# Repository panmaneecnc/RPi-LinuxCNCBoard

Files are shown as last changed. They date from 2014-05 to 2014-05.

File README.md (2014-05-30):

RPi-LinuxCNCBoard
=================
These files are part of the rpi_rboq project.
driver: Contains all the files related with the HAL(Hardware Abstraction Layer) driver programmed to integrate rpi_rboq to LinuxCNC.
PCB: Contains all the files of the PCB design. To open this files you required Eagle 6.5.0 version, available from: http://www.cadsoftusa.com/
presentation: Contain the presentation designed for oral defense.
raspberry_images: Contains the images compiled during the work using Xenomai and the PREEMPT-RT patch.
report: Contain the full report in PDF format.
testing: Contain all the testing code and libraries written by this work.

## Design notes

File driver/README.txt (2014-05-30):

To install this driver, execute the following command in Linux console:
sudo comp --install --install-documentation hal_rpirboq.hal

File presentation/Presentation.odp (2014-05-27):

## Beijing University of Posts and Telecommunications 北京邮电大学

CONTROL BOARD FOR CNC SYSTEMS BASED IN LINUX

Author: Rodolfo Boris Oporto Quisbert

Final Project

## Contents

- 1 Introduction
- 2 Background and technologies
- 3 Design and implementation
- 4 Results
- 5 Conclusions and future work

## 1 Introduction

- Project motivation
  - Try to make a fully functional control board for CNC systems.
    - In the last years, this systems have attracted the attention of many groups, interested especially in 3D printers.
  - Research about Open Source solutions a its characteristics.
    - Raspberry-Pi, LinuxCNC, Xenomai, RepRap, Raspbian.

## 2 Background

- Raspberry Pi
  - Raspberry-Pi is a low cost fully-functional computer, based in BCM2835 SoC from Broadcom.
  - This board was developed to be used as part of an educational program in UK.

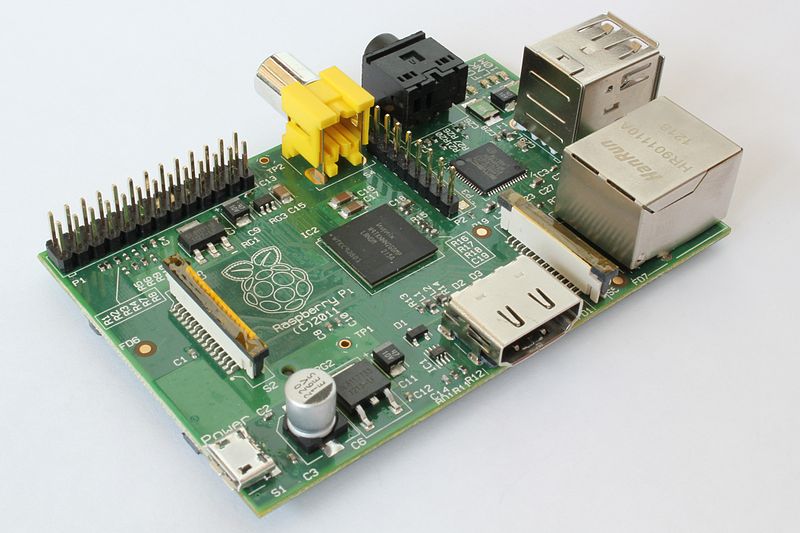
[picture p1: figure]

## 2 Background

- Raspberry Pi
  - Low cost (~300RMB)
  - Huge community.
    - Support.
    - Docummentation.
      - Blogs, papers, internet forums, books.

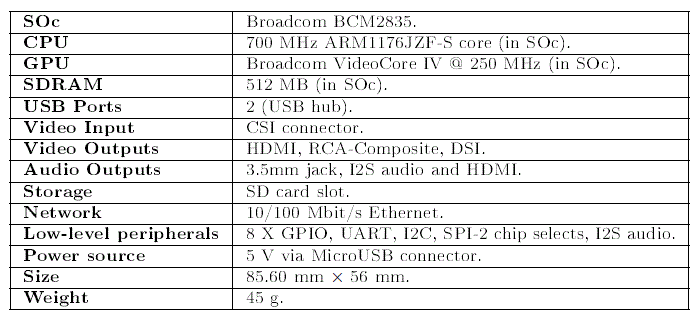
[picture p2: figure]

## 2 Background

- Real time under Linux
  - PREEMPT_RT patch
    - Preemption: Preemption is the interruption of a computer process without its cooperation
    - How does it work?
      - Making in-kernel locking-primitives.
      - Critical sections protected.
      - Implementing priority.

## 2 Background

- Real time under Linux
  - Xenomai
    - Xenomai is a real-time development framework cooperating with the Linux kernel.
    - API skins: native, POXIS, RTDM, pSOS
    - Two spaces
      - Kernel space: Hard real-time applications
      - User space: Real-time applications

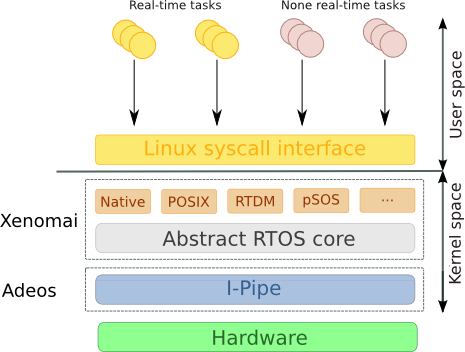
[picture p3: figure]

## 2 Background

- Real time under Linux
  - Why Xenomai?
    - Xenomai has a well documented API with different skins.
      - Examples, internet forums, API html documentation.
    - There is experiences with Xenomai running in Raspberry-Pi and LinuxCNC.
    - Official Xenomai patch for Raspberry-Pi.

## 2 Background

- LinuxCNC
  - Software collection for CNC machines. Former know as EMC.
  - Hardware Abstraction Layer
    - LinuxCNC use software components know as Hardware Abstraction Layer (HAL)
    - The developer can abstract from the details inside these blocks and use it like Symulink block.

## 2 Background

- LinuxCNC
  - Hardware Abstraction Layer
    - Some very important HAL components
      - RT Threads: hard real time thread which can be used to perform HAL functions at specific time
      - Stepgen: This component allow to control stepper-motors, generating all the signals required.
      - PID: This component implements a PID control block.
      - PWMgen: This component generate a PWM signal.

## 2 Background

- RepRap - 3D printer
  - RepRap is an Open Source project which starts in 2005, in the University of Bath, in UK by Adrian Bowyer. The aim of RepRap project was to create a 3D printer cheaper than the commercial ones, and the most important, a self-replicant 3D printer.

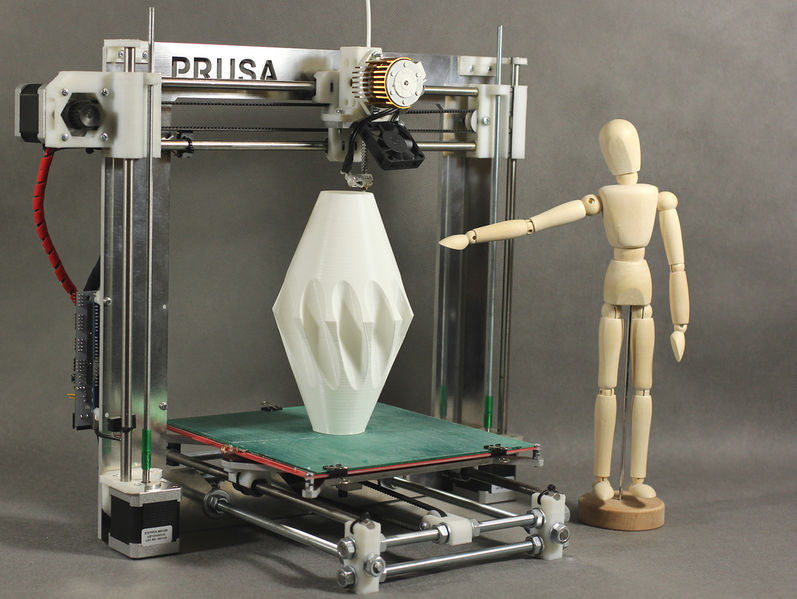
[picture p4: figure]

## 3 Design and implementation

- Board description
  - ADC: The core of the ADC system is the ADS8556 from Texas Instruments. This device has six channels, 16 bit's resolution, fully bipolar inputs, with serial or parallel communication. This device use SAR as conversion method. And the communication is through SPI.

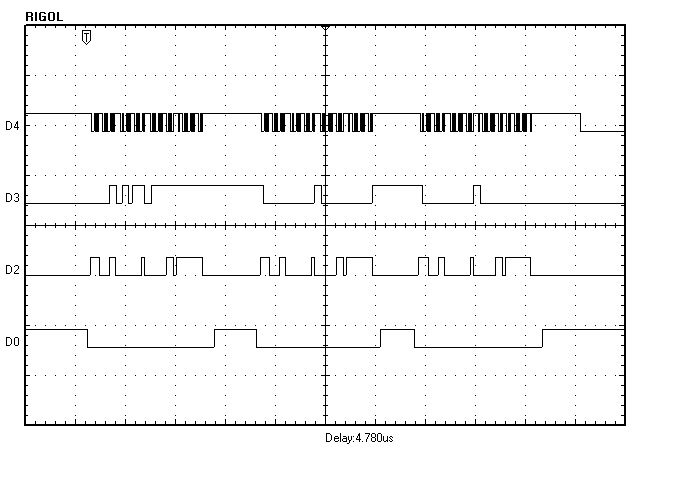
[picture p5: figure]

## 3 Design and implementation

- Board description
  - ADC
    - Sample and hold subcircuit.
    - Voltage reference for resistive transductors

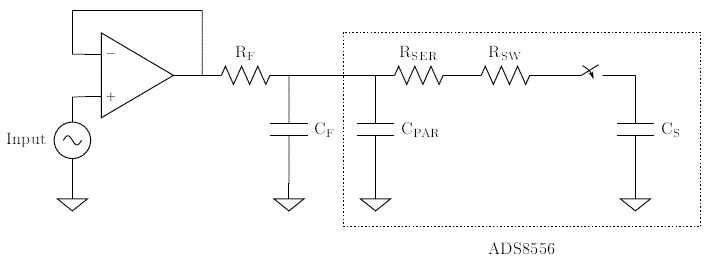
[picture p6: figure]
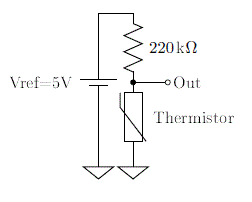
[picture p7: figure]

## 3 Design and implementation

- Board description
  - PWM: In this work was required N-MOSFET IRF630B to supply enough energy to components such as heaters and servomotors.

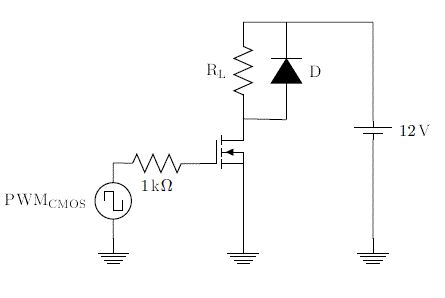
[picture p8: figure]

## 3 Design and implementation

- Board description
  - Steppers drivers: To control the stepper-motors, we use the A4983. A4983 is an integrated driver that just require the STEP and DIR signals.

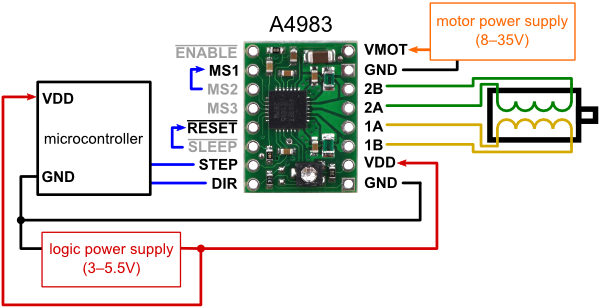
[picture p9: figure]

## 3 Design and implementation

- Board description
  - MCP23S17 from Microchip.
    - 16 bidirectional I/O.
    - Control by interruption.
    - SPI communication.

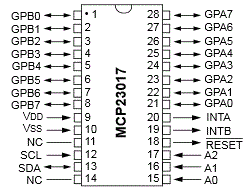
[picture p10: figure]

## 3 Design and implementation

- HAL Driver
  - HAL is the highest level of a component in LinuxCNC. It means that any complex system is composed by several HAL blocks.
  - In this work was implemented a HAL component that controls the board.

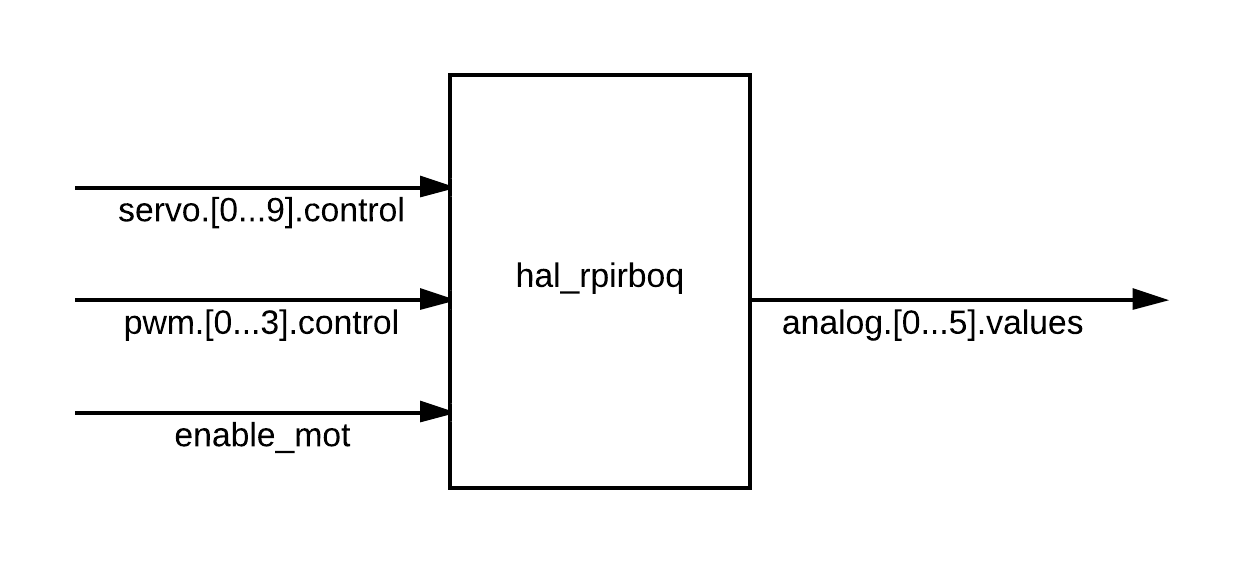
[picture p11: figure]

## 4 Results

- Latency test
  - This test start two real-time threads and perform testing real-time functions.
  - The user interface present the average of latency in both, and the most important the maximum jitter value that can be interpreted as the minimum period that can be used to execute real-time functions.

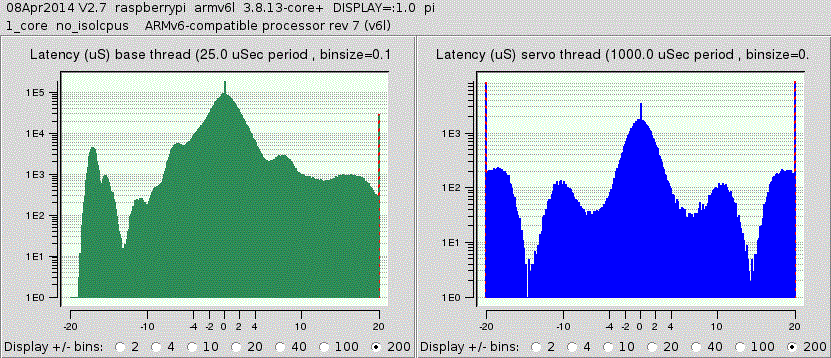
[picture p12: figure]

## 4 Results

- Board tests
  - ADC test
    - samples_cvs.c
  - PWM test
    - pwm_test in LinuxCNC

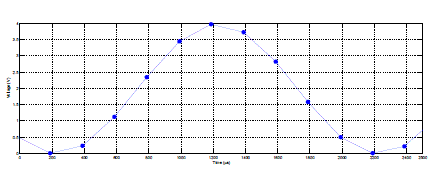
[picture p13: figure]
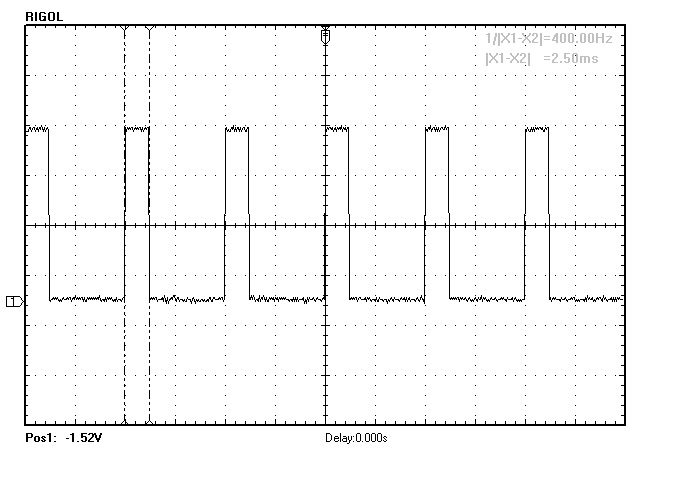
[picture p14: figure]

## 4 Results

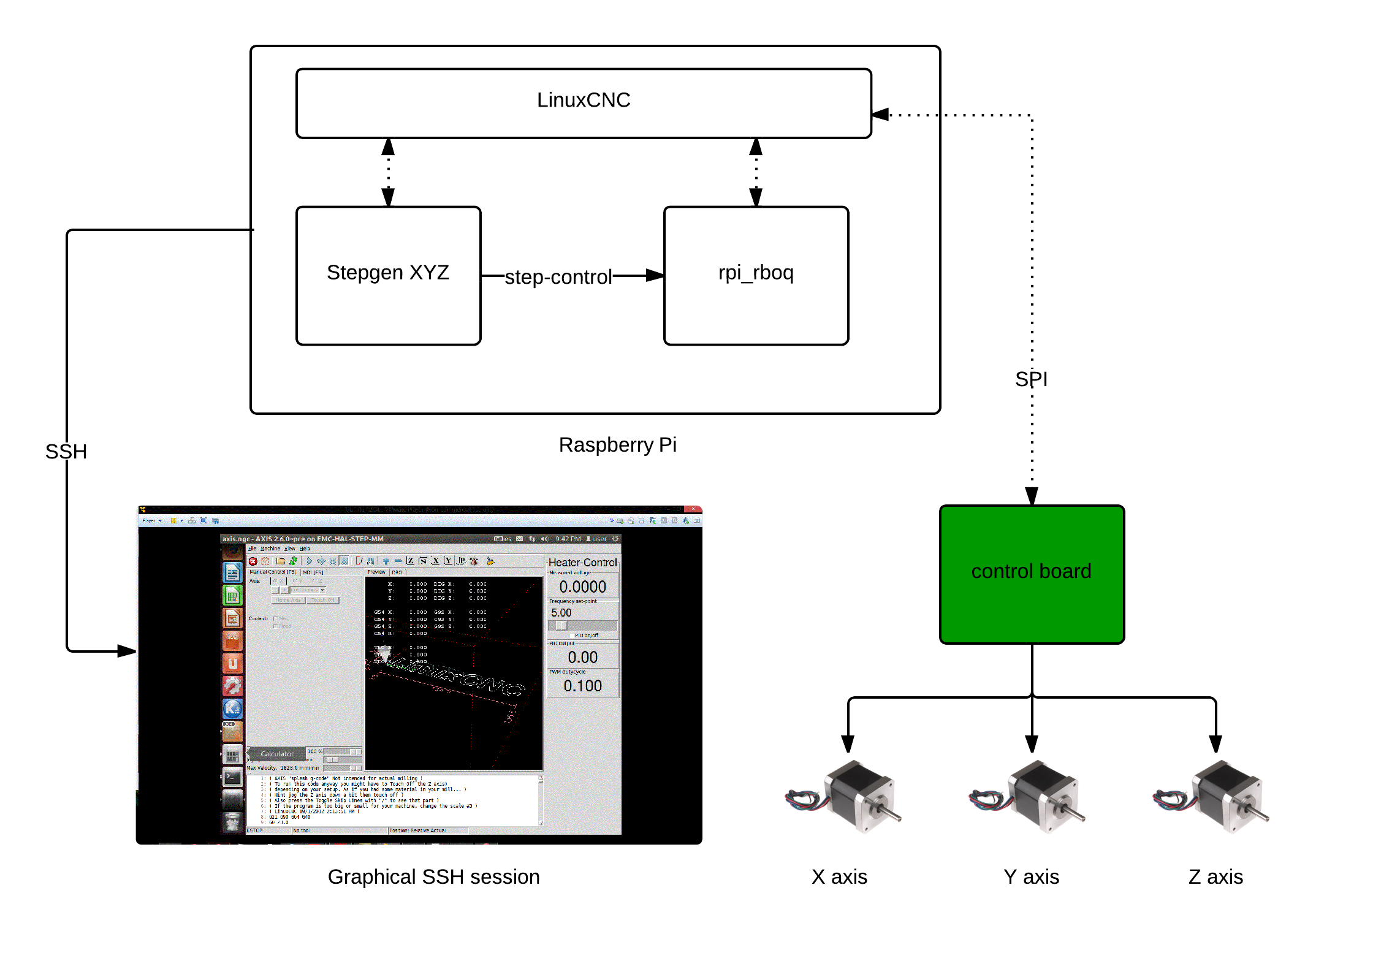
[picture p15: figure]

## 4 Results

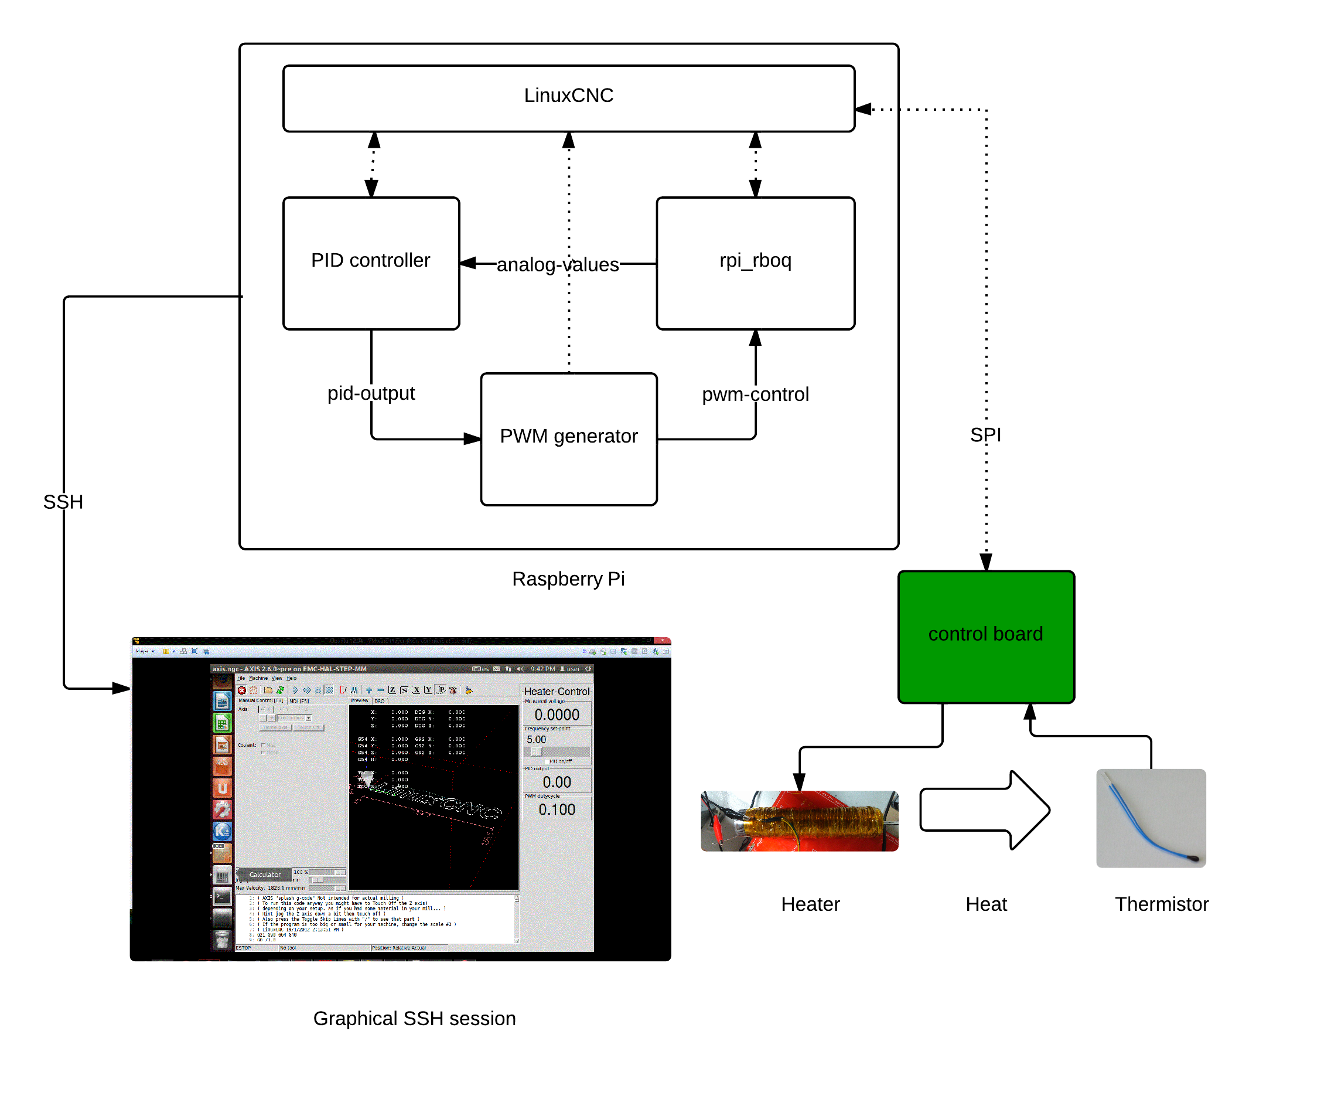
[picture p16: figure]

## 5 Conclusions and future work

- Conclusions and results discussion
  - In general, the board designed, achieved a good integration with others blocks.
  - We found some speed lilmitations due to the maximum jitter provided by Raspberry-Pi
    - PWM maximum frequency 200Hz.
    - Maximum stepps 200 steps/second.
    - ADC maximum input signal frequency 10kHz
- Future work

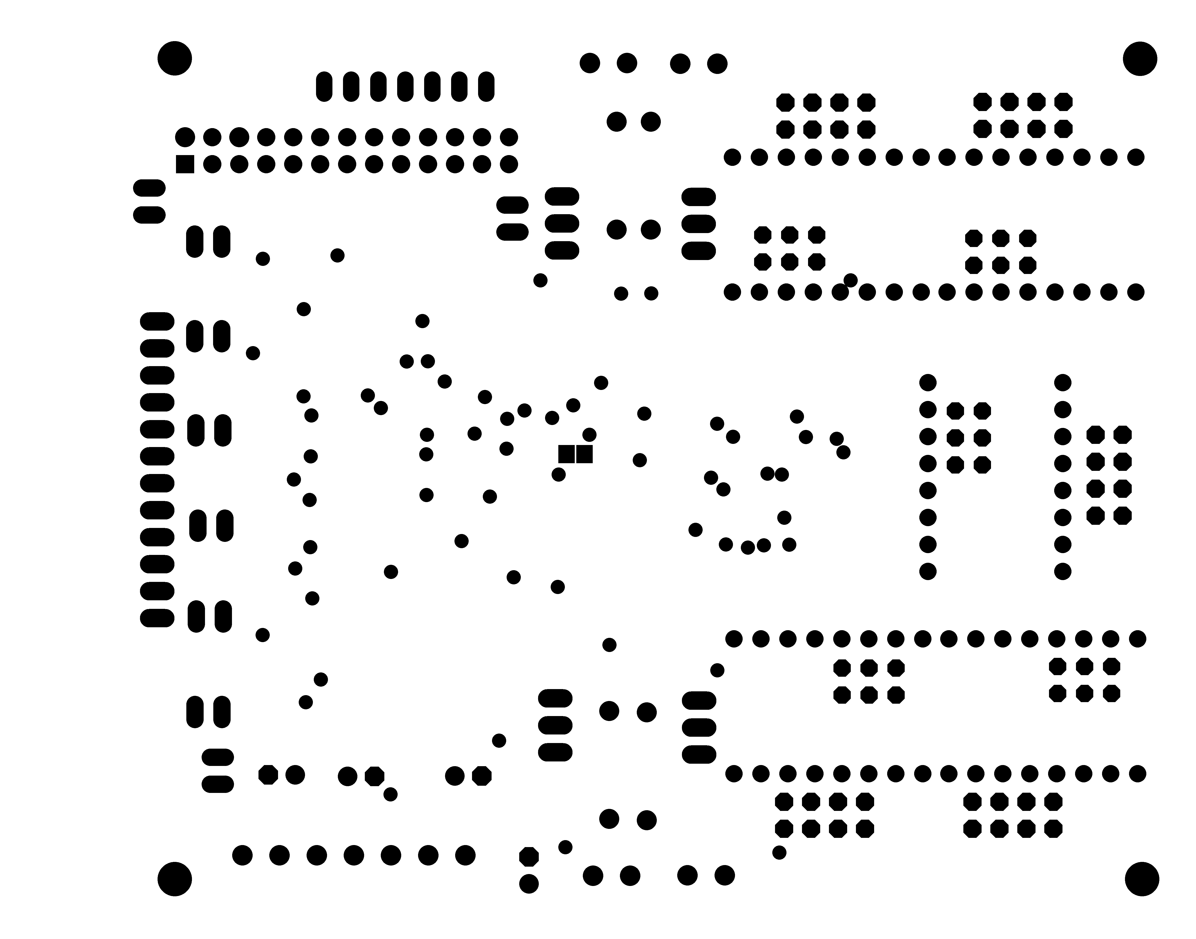
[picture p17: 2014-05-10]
PCB/rpi_rboq/eagleUp/eagleUp_raspi_reprap_bottom_mask.png

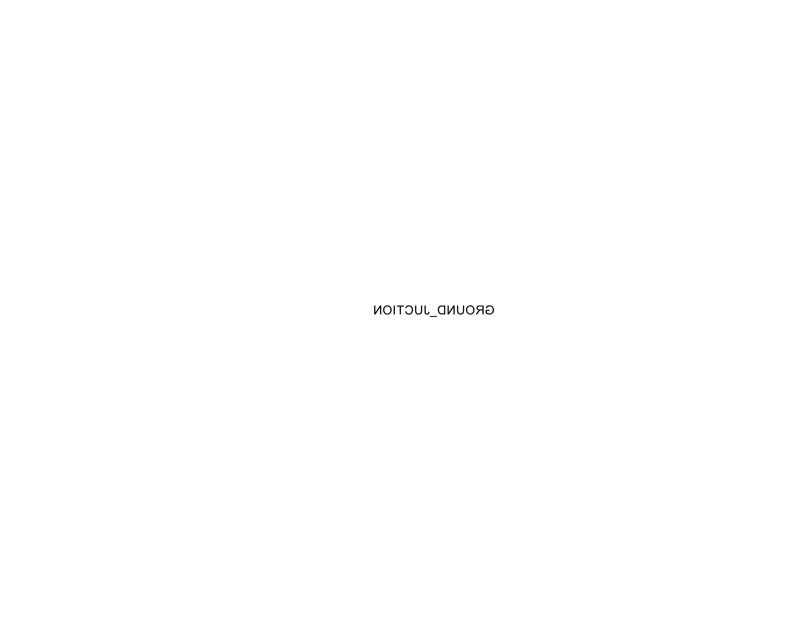
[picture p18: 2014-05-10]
PCB/rpi_rboq/eagleUp/eagleUp_raspi_reprap_bottom_silk.png

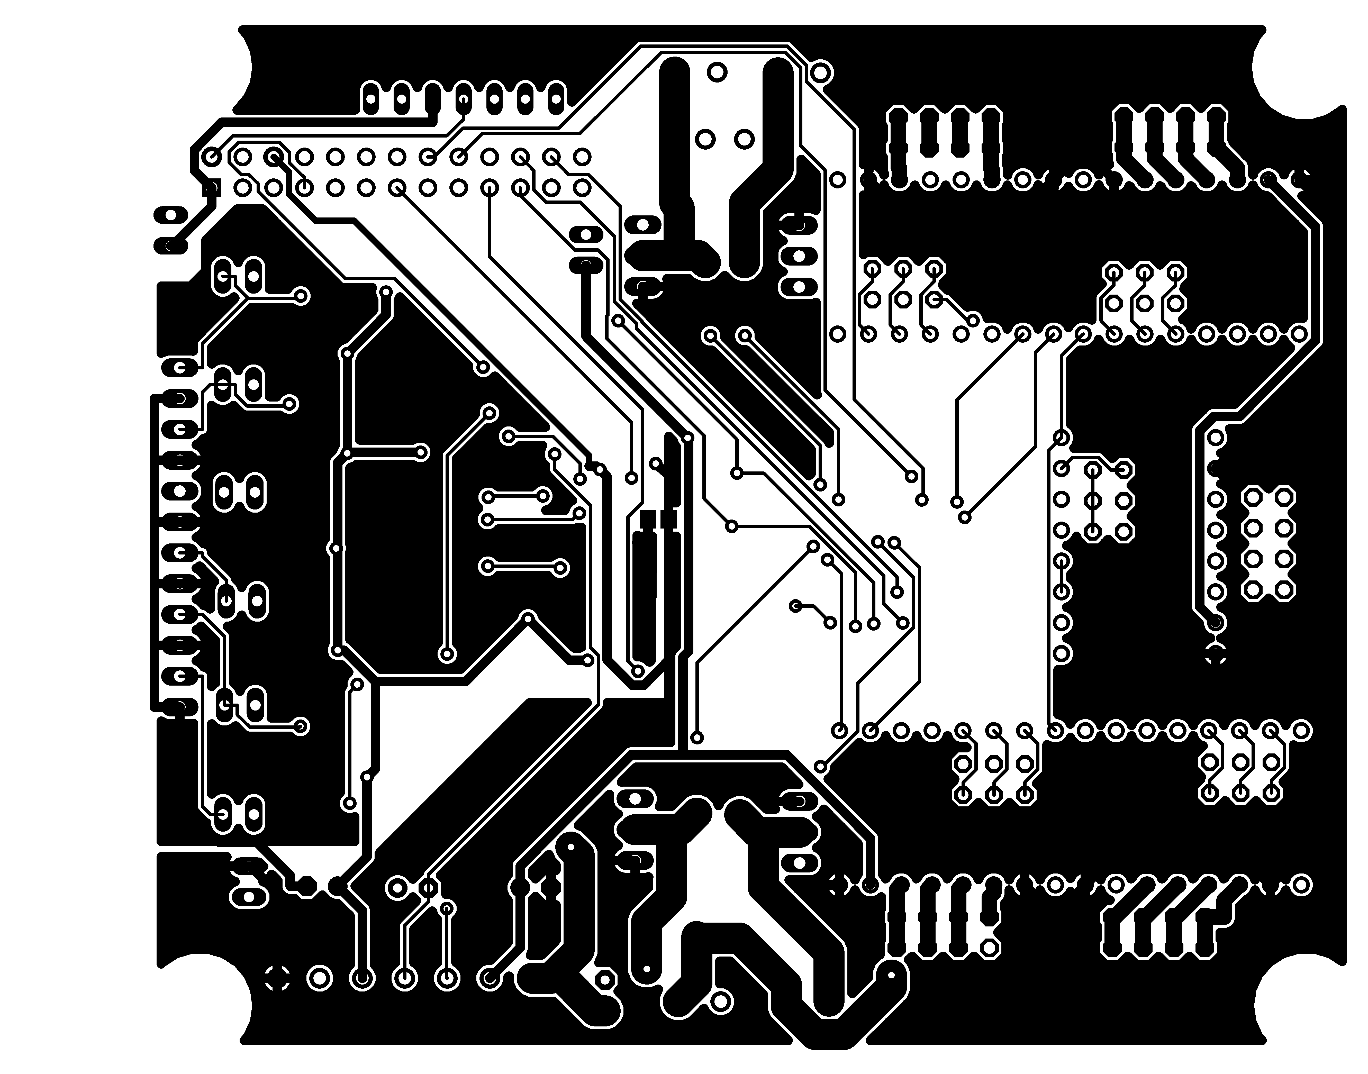
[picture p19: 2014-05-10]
PCB/rpi_rboq/eagleUp/eagleUp_raspi_reprap_bottom.png

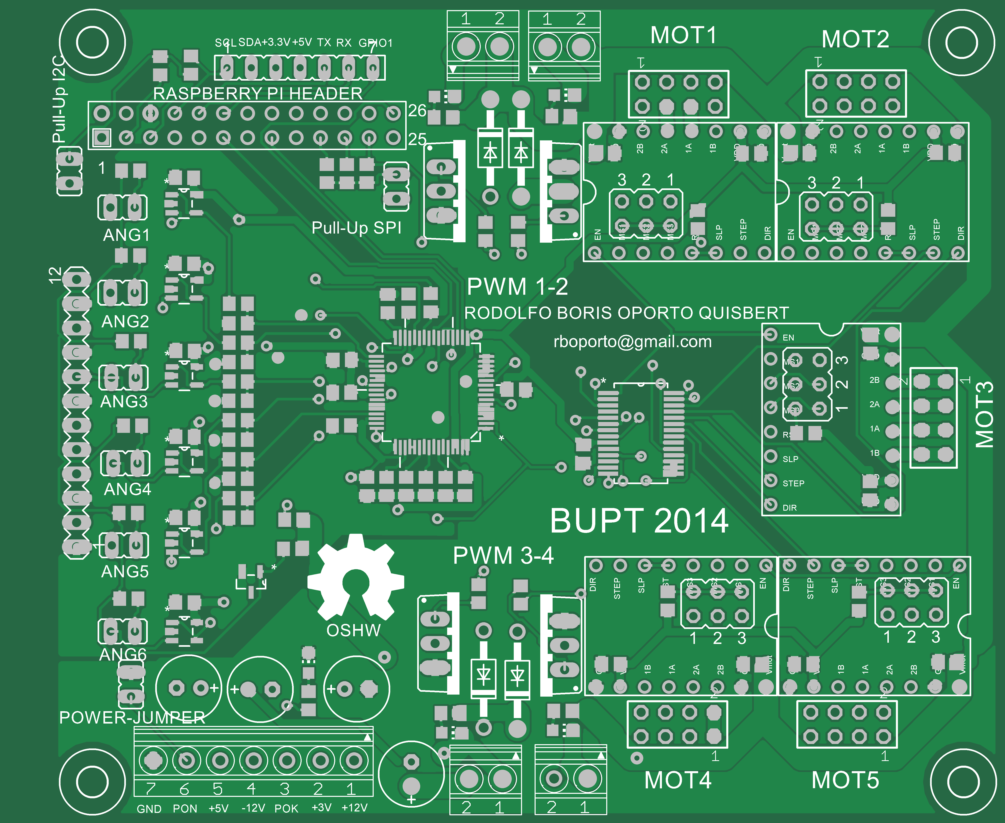
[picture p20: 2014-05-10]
PCB/rpi_rboq/eagleUp/eagleUp_raspi_reprap_board_top.png

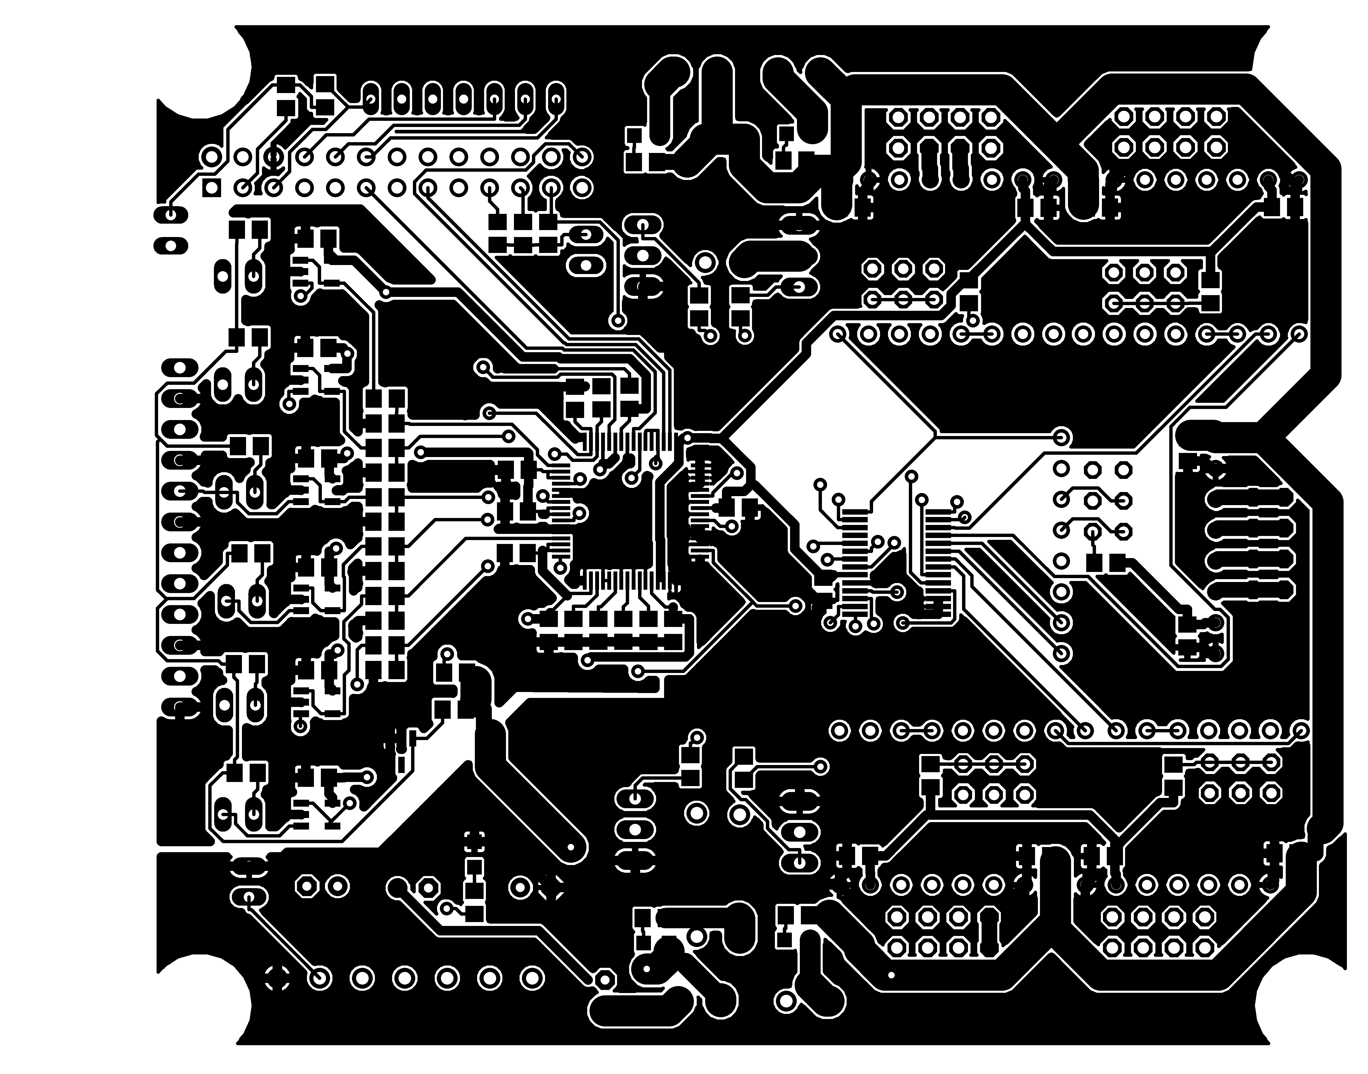
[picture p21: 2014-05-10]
PCB/rpi_rboq/eagleUp/eagleUp_raspi_reprap_top.png

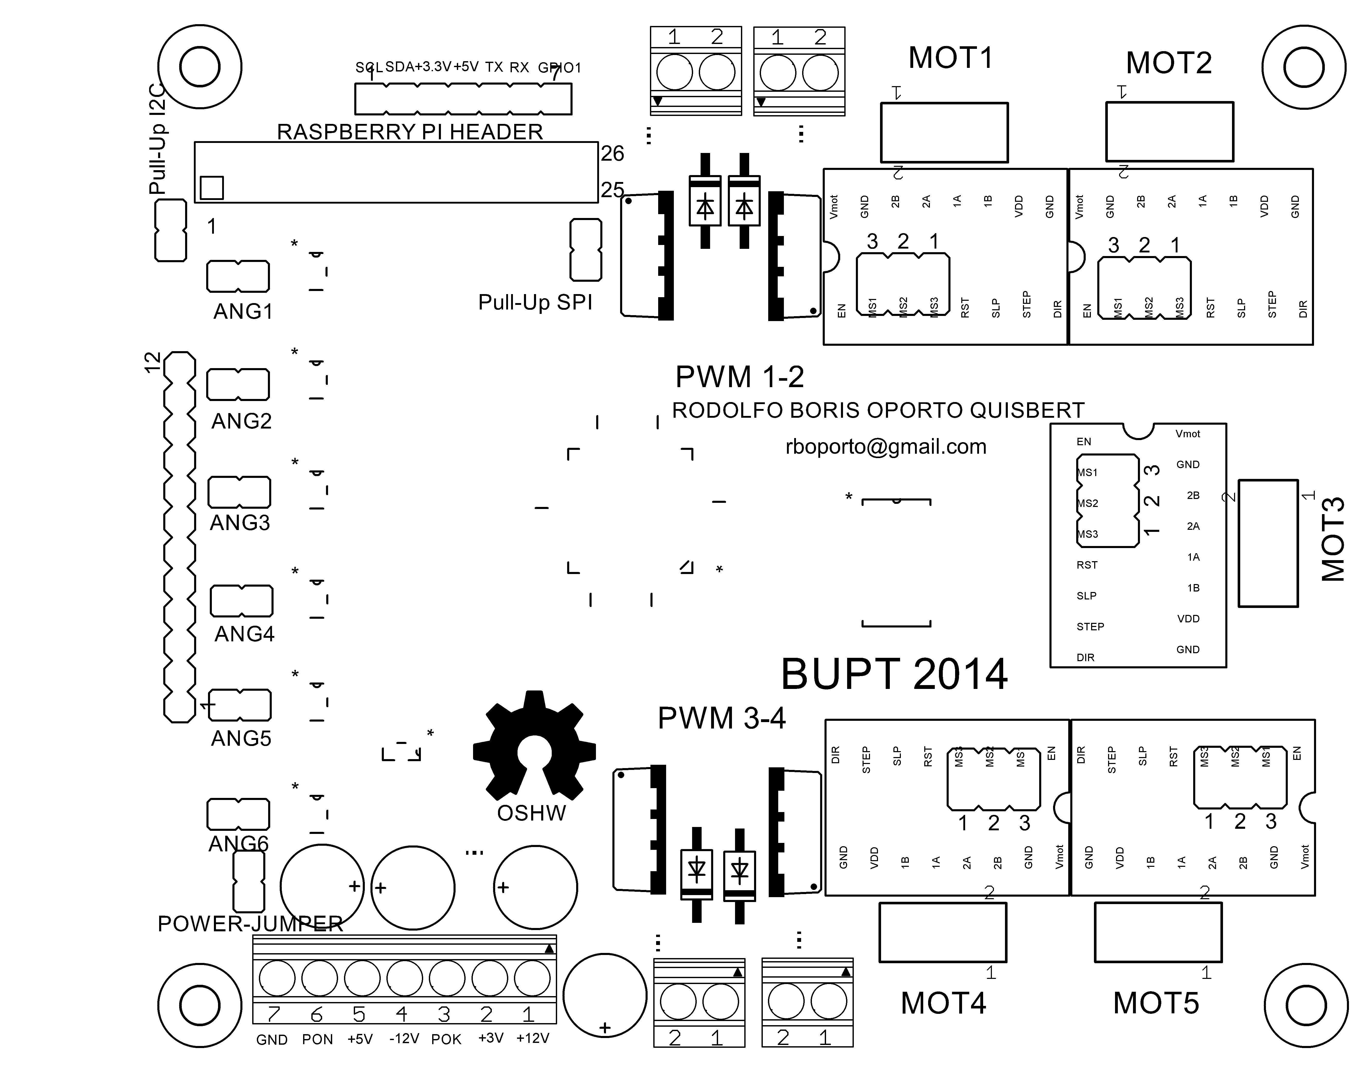
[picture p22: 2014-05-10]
PCB/rpi_rboq/eagleUp/eagleUp_raspi_reprap_top_silk.png

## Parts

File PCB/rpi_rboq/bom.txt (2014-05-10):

Partlist exported from C:/Users/rboq/Documents/eagle/ADC/raspi_reprap.sch at 12/2/2013 4:26:29 PM

Qty Value          Device           Package                 Parts                                               Description                                               
6                  JP1E             JP1                     JP1, JP2, JP3, JP4, JP5, JP6                        JUMPER                                                    
5                  JP2Q             JP2Q                    JP7, JP8, JP9, JP10, JP11                           JUMPER                                                    
1                  LEDCHIP-LED0805  CHIP-LED0805            LED1                                                LED                                                       
4                  PMOSFET_NTO220BV TO220BV                 Q1, Q2, Q3, Q4                                      Power MOSFET N-Channel                                    
2                  R-EU_R0805       R0805                   R2, R16                                             RESISTOR, European symbol                                 
4   +12            1751248          1751248                 TM, TM1, TM2, TM3                                   MKDS 1/ 2-3,5 Printklemme                                 
1   0              R-EU_R0805       R0805                   C13                                                 RESISTOR, European symbol                                 
12  100nF          C-EUC0201        C0201                   C1, C2, C5, C6, C7, C8, C9, C11, C12, C14, C39, C41 CAPACITOR, European symbol                                
6   100nF          C-EUC0402        C0402                   C16, C17, C19, C20, C21, C22                        CAPACITOR, European symbol                                
10  100nF          C-EUC0805        C0805                   C29, C30, C31, C32, C33, C34, C35, C36, C37, C38    CAPACITOR, European symbol                                
3   10uF           C-EUC0201        C0201                   C10, C15, C18                                       CAPACITOR, European symbol                                
4   10uF           C-EUC0805        C0805                   C40, C42, C43, C44                                  CAPACITOR, European symbol                                
6   120k           R-EU_R0805       R0805                   R3, R4, R5, R6, R7, R8                              RESISTOR, European symbol                                 
6   1751248        1751248          1751248                 ANG1, ANG2, ANG3, ANG4, ANG5, ANG6                  MKDS 1/ 2-3,5 Printklemme                                 
5   1751264        1751264          1751264                 X2, X3, X4, X5, X6                                  MKDS 1/ 4-3,5 Printklemme                                 
1   1751293        1751293          1751293                 X1                                                  MKDS 1/ 7-3,5 Printklemme                                 
9   1k             R-EU_R0805       R0805                   R17, R18, R19, R20, R21, R22, R23, R24, R25         RESISTOR, European symbol                                 
1   1uF            C-EUC0201        C0201                   C4                                                  CAPACITOR, European symbol                                
6   43             R-EU_R0805       R0805                   R9, R10, R11, R12, R13, R14                         RESISTOR, European symbol                                 
1   470nF          C-EUC0201        C0201                   C3                                                  CAPACITOR, European symbol                                
6   470pF          C-EUC0805        C0805                   C23, C24, C25, C26, C27, C28                        CAPACITOR, European symbol                                
5   A4983CARRIER   A4983CARRIER     A4988BREAKOUT           U$2, U$3, U$4, U$5, U$6                                                                                       
1   ADS8556IPM     ADS8556IPM       QFP50P1200X1200X160-64N U8                                                  ANALOG-TO-DIGITAL CONVERTERS                              
1   LM4040D50IDBZR LM4040D50IDBZR   SOT95P237X112-3N        U1                                                  PRECISION MICROPOWER SHUNT VOLTAGE REFERENCE              
1   MCP23S17-E/SS  MCP23S17-E/SS    SOP65P780X200-28N       U9                                                  IC, 16-Bit I/O Expander with Serial Interface,    SSOP-28 
6   OPA365AIDBVTG4 OPA365AIDBVTG4   SOT95P280X145-5N        U2, U3, U4, U5, U6, U7                              OPERATIONAL AMPLIFIER                                     
1   RASPBERRY-PI   RASPBERRY-PI     RASPBERRY-PI            U$1                                                 Raspberry Pi Board                                        
4   TPB1,27        TPB1,27          B1,27                   TP1, TP2, TP3, TP4                                  Test pad

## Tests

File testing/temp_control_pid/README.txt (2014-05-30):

These scripts start the LinuxCNC enviroment using the rpi_rboq board.

These scripts are based in steppeconfig autogenerated code.

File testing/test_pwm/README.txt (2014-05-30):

To run this test tipe the following command. 
halrun -I hal-test.hal

Part of this code is based in RC Servo Test code available from here: http://wiki.linuxcnc.org/cgi-bin/wiki.pl?RC_Servo_Test

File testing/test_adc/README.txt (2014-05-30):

To compile the test, you have to invoke the MAKEFILE using the command make.

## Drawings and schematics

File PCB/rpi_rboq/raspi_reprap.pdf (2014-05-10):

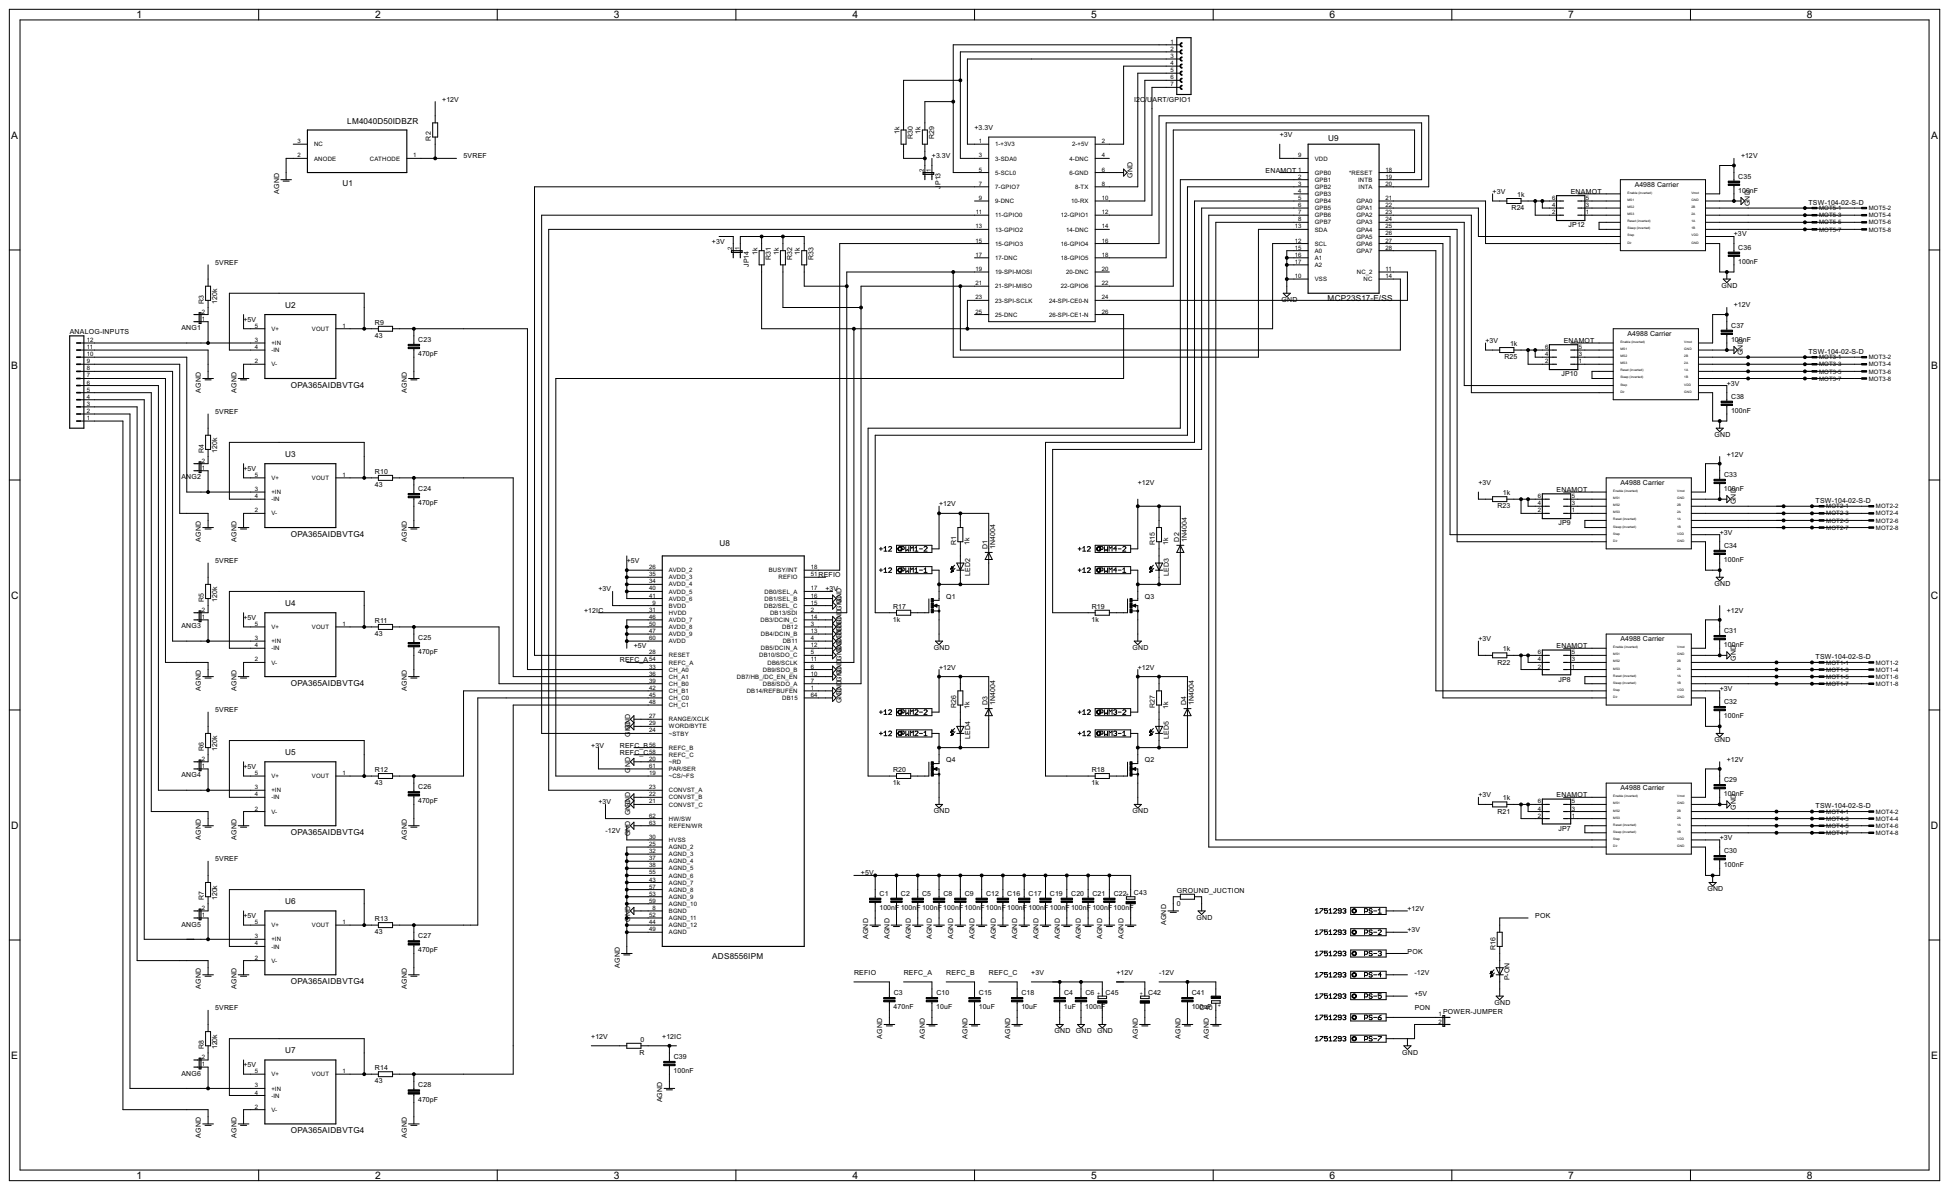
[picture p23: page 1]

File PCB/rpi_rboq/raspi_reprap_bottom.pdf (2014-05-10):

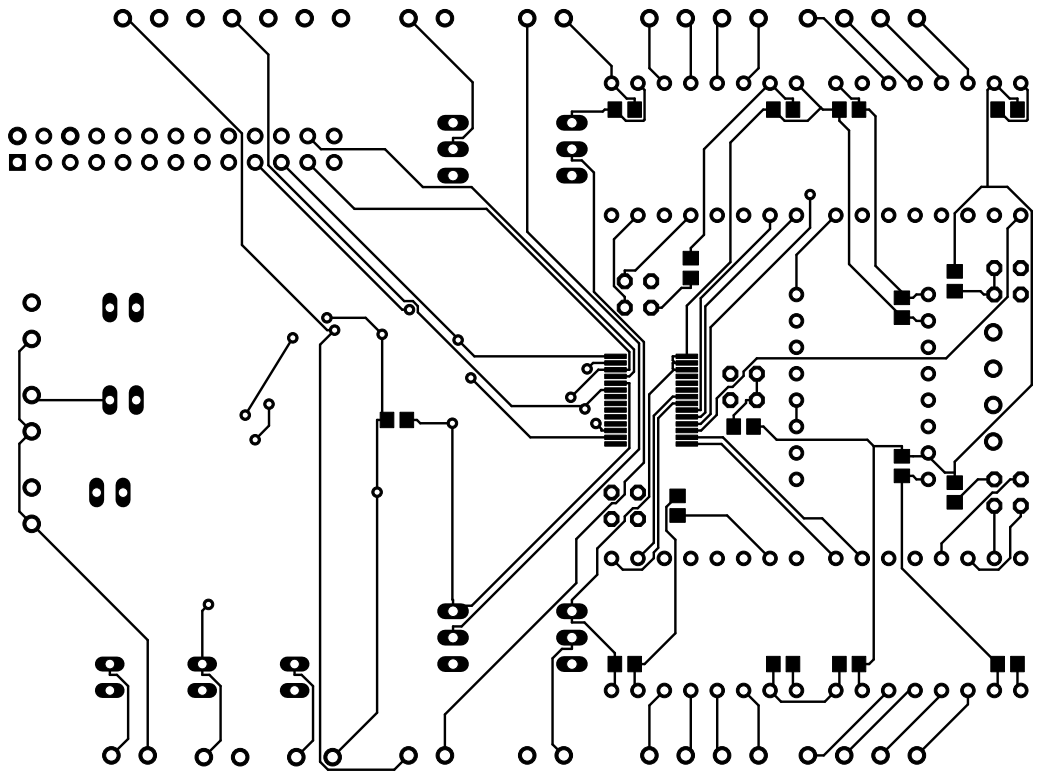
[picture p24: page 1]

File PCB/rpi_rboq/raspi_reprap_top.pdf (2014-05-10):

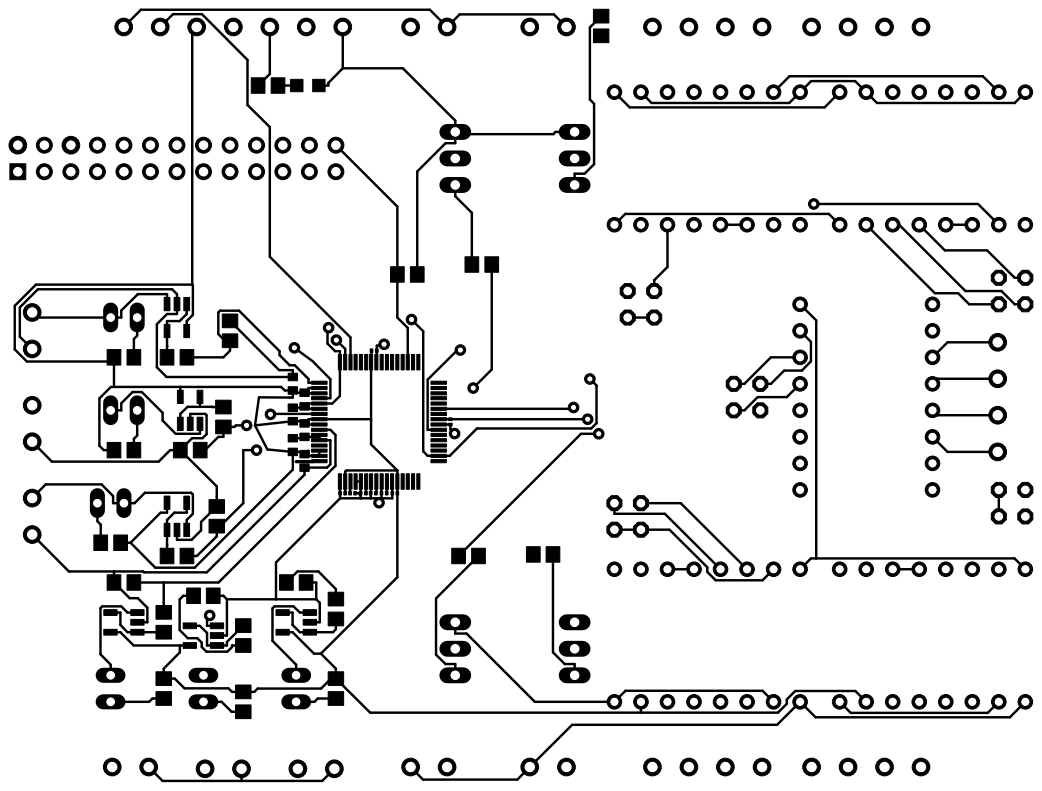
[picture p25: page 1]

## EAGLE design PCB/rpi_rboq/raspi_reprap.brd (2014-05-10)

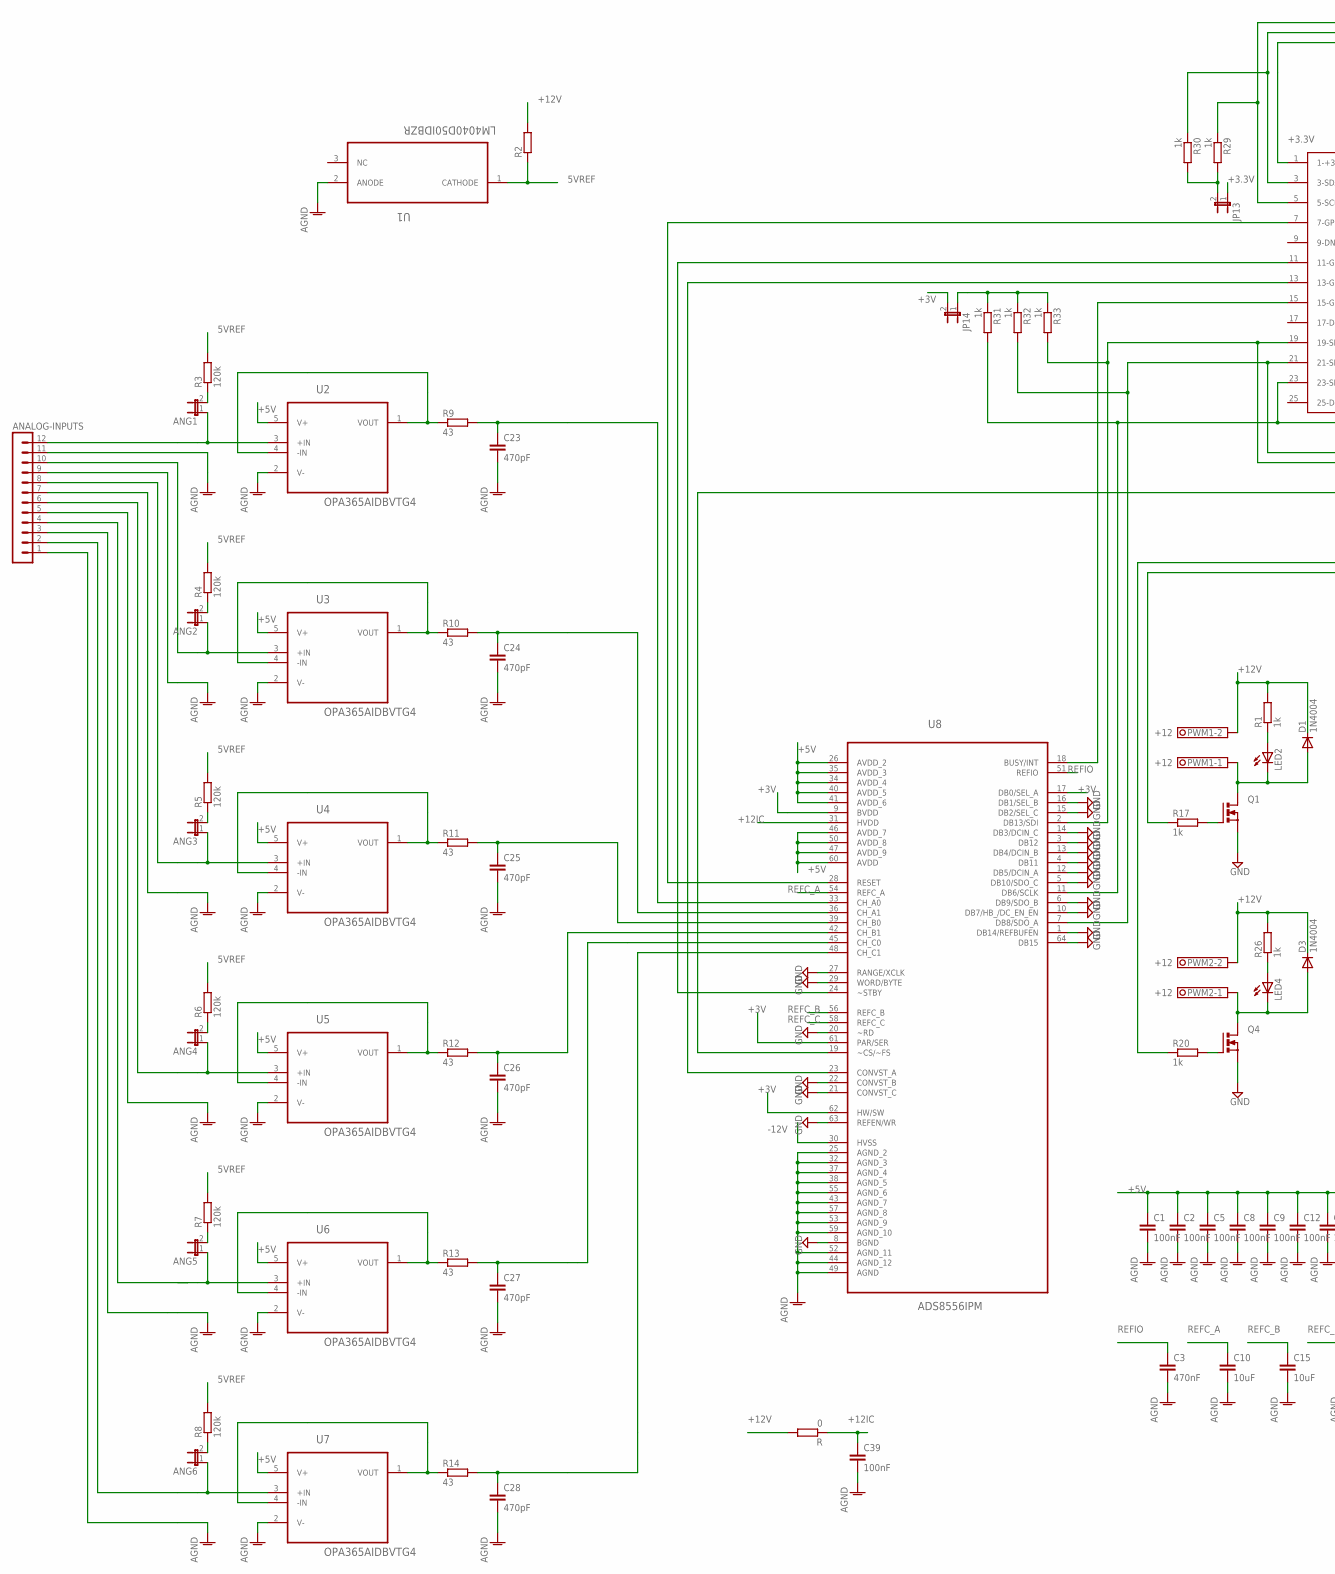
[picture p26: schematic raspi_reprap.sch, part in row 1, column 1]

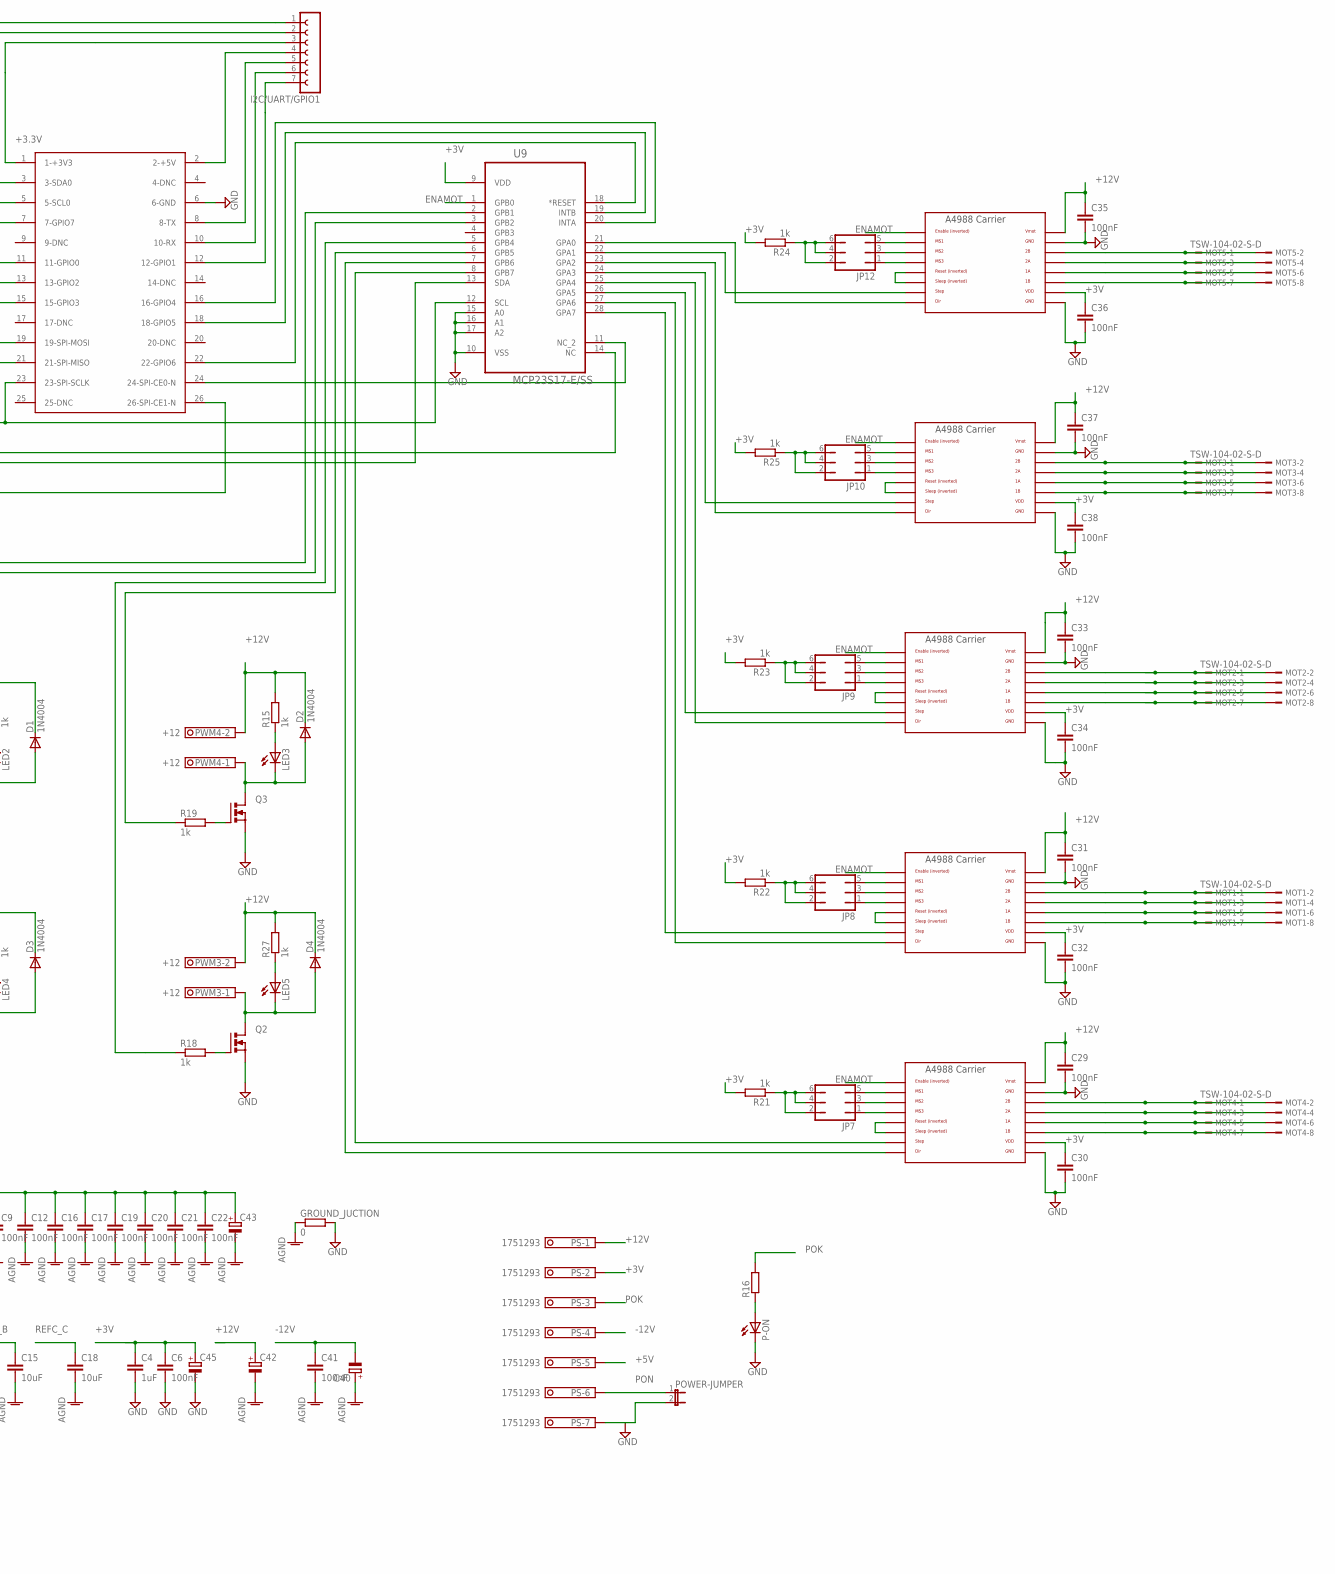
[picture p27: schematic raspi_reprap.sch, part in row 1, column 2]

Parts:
ANALOG-INPUTS: MA12-1
ANG1, ANG2, ANG3, ANG4, ANG5, ANG6: JP1E; JP1
C1, C2, C5, C6, C8, C9, C12, C16, C17, C19, C20, C21, C22, C29, C30, C31, C32, C33, C34, C35, C36, C37, C38, C39, C41: 100nF; C0805
C3: 470nF; C0805
C4: 1uF; C0805
C10, C15, C18: 10uF; C0805
C23, C24, C25, C26, C27, C28: 470pF; C0805
C40, C42, C43, C45: CPOL-EUE2.5-7; E2,5-7
D1, D2, D3, D4: 1N4004; DO41-10
GROUND_JUCTION: 0; R0805
I2C/UART/GPIO1: FE07-1; FE07
JP7, JP8, JP9, JP10, JP12: JP3Q
JP13, JP14: JP1E; JP1
LED2, LED3, LED4, LED5: LEDCHIP-LED0805; CHIP-LED0805
MOT1, MOT2, MOT3, MOT4, MOT5: TSW-104-02-S-D
P-ON: LEDCHIP-LED0805; CHIP-LED0805
POWER-JUMPER: JP1E; JP1
PS: 1751293
PWM1, PWM2, PWM3, PWM4: +12; 1751248
Q1, Q2, Q3, Q4: PMOSFET_NTO220BV; TO220BV
R: 0; R0805
R1, R15, R17, R18, R19, R20, R21, R22, R23, R24, R25, R26, R27, R29, R30, R31, R32, R33: 1k; R0805
R2, R16: R-EU_R0805; R0805
R3, R4, R5, R6, R7, R8: 120k; R0805
R9, R10, R11, R12, R13, R14: 43; R0805
RPI-HEADER: RASPBERRY-PI
U1: LM4040D50IDBZR; SOT95P237X112-3N
U2, U3, U4, U5, U6, U7: OPA365AIDBVTG4; SOT95P280X145-5N
U8: ADS8556IPM; QFP50P1200X1200X160-64N
U9: MCP23S17-E/SS; SOP65P780X200-28N
U$2, U$3, U$4, U$5, U$6: A4983CARRIER; A4988BREAKOUT

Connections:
5VREF: R2.1, R3.2, R4.2, R5.2, R6.2, R7.2, R8.2, U1.1 (CATHODE)
+3.3V: I2C/UART/GPIO1.3, JP13.1, RPI-HEADER.1 (1-+3V3)
+3V: C4.1, C6.1, C30.1, C32.1, C34.1, C36.1, C38.1, C45.+, JP14.2, PS.2, R21.2, R22.2, R23.2, R24.2, R25.2, U8.9 (BVDD), U8.17 (DB0/SEL_A), U8.61 (PAR/SER), U8.62 (HW/SW), U9.9 (VDD), U$2.VDD, U$3.VDD, U$4.VDD, U$5.VDD, U$6.VDD
+5V: C1.1, C2.1, C5.1, C8.1, C9.1, C12.1, C16.1, C17.1, C19.1, C20.1, C21.1, C22.1, C43.+, PS.5, U2.5 (V+), U3.5 (V+), U4.5 (V+), U5.5 (V+), U6.5 (V+), U7.5 (V+), U8.26 (AVDD_2), U8.34 (AVDD_4), U8.35 (AVDD_3), U8.40 (AVDD_5), U8.41 (AVDD_6), U8.46 (AVDD_7), U8.47 (AVDD_9), U8.50 (AVDD_8), U8.60 (AVDD)
+12IC: C39.1, R.1, U8.31 (HVDD)
+12V: C29.1, C31.1, C33.1, C35.1, C37.1, C42.+, D1.C, D2.C, D3.C, D4.C, PS.1, PWM1.2, PWM2.2, PWM3.2, PWM4.2, R.2, R1.2, R2.2, R15.2, R26.2, R27.2, U$2.VMOT, U$3.VMOT, U$4.VMOT, U$5.VMOT, U$6.VMOT
-12V: C40.-, C41.1, PS.4, U8.30 (HVSS)
AGND: ANALOG-INPUTS.1, ANALOG-INPUTS.3, ANALOG-INPUTS.5, ANALOG-INPUTS.7, ANALOG-INPUTS.9, ANALOG-INPUTS.11, C1.2, C2.2, C3.2, C5.2, C8.2, C9.2, C10.2, C12.2, C15.2, C16.2, C17.2, C18.2, C19.2, C20.2, C21.2, C22.2, C23.2, C24.2, C25.2, C26.2, C27.2, C28.2, C39.2, C40.+, C41.2, C42.-, C43.-, GROUND_JUCTION.1, U1.2 (ANODE), U2.2 (V-), U3.2 (V-), U4.2 (V-), U5.2 (V-), U6.2 (V-), U7.2 (V-), U8.25 (AGND_2), U8.32 (AGND_3), U8.37 (AGND_4), U8.38 (AGND_5), U8.43 (AGND_7), U8.44 (AGND_12), U8.49 (AGND), U8.52 (AGND_11), U8.53 (AGND_9), U8.55 (AGND_6), U8.57 (AGND_8), U8.59 (AGND_10)
CE1: RPI-HEADER.24 (24-SPI-CE0-N), U9.11 (NC_2)
CE2: RPI-HEADER.26 (26-SPI-CE1-N), U8.19 (~CS/~FS)
CLK: R31.2, RPI-HEADER.23 (23-SPI-SCLK), U8.11 (DB6/SCLK), U9.12 (SCL)
ENAMOT: U9.1 (GPB0), U$2.EN, U$3.EN, U$4.EN, U$5.EN, U$6.EN
GND: C4.2, C6.2, C29.2, C30.2, C31.2, C32.2, C33.2, C34.2, C35.2, C36.2, C37.2, C38.2, C45.-, GROUND_JUCTION.2, P-ON.C, POWER-JUMPER.2, PS.7, Q1.S, Q2.S, Q3.S, Q4.S, RPI-HEADER.6 (6-GND), U8.1 (DB14/REFBUFEN), U8.3 (DB12), U8.4 (DB11), U8.5 (DB10/SDO_C), U8.6 (DB9/SDO_B), U8.8 (BGND), U8.10 (DB7/HB_/DC_EN_EN), U8.12 (DB5/DCIN_A), U8.13 (DB4/DCIN_B), U8.14 (DB3/DCIN_C), U8.15 (DB2/SEL_C), U8.16 (DB1/SEL_B), U8.20 (~RD), U8.21 (CONVST_C), U8.22 (CONVST_B), U8.27 (RANGE/XCLK), U8.29 (WORD/BYTE), U8.63 (REFEN/WR), U8.64 (DB15), U9.10 (VSS), U9.15 (A0), U9.16 (A1), U9.17 (A2), U$2.GND, U$2.GND@0 (GND), U$3.GND, U$3.GND@0 (GND), U$4.GND, U$4.GND@0 (GND), U$5.GND, U$5.GND@0 (GND), U$6.GND, U$6.GND@0 (GND)
GPIO1: I2C/UART/GPIO1.7, RPI-HEADER.12 (12-GPIO1)
M1-MOT2: MOT4.3, MOT4.4, U$2.2A
M1-MOT3: MOT4.5, MOT4.6, U$2.1A
M1-MOT4: MOT4.7, MOT4.8, U$2.1B
M2-MOT1: MOT1.1, MOT1.2, U$3.2B
M2-MOT2: MOT1.3, MOT1.4, U$3.2A
M2-MOT3: MOT1.5, MOT1.6, U$3.1A
M2-MOT4: MOT1.7, MOT1.8, U$3.1B
M3-MOT1: MOT2.1, MOT2.2, U$4.2B
M3-MOT2: MOT2.3, MOT2.4, U$4.2A
M3-MOT3: MOT2.5, MOT2.6, U$4.1A
M3-MOT4: MOT2.7, MOT2.8, U$4.1B
M4-MOT1: MOT5.1, MOT5.2, U$5.2B
M4-MOT2: MOT5.3, MOT5.4, U$5.2A
M4-MOT3: MOT5.5, MOT5.6, U$5.1A
M4-MOT4: MOT5.7, MOT5.8, U$5.1B
M5-MOT1: MOT3.1, MOT3.2, U$6.2B
M5-MOT2: MOT3.3, MOT3.4, U$6.2A
M5-MOT3: MOT3.5, MOT3.6, U$6.1A
M5-MOT4: MOT3.7, MOT3.8, U$6.1B
MISO: R32.2, RPI-HEADER.21 (21-SPI-MISO), U8.7 (DB8/SDO_A), U9.14 (NC)
MOSI: R33.2, RPI-HEADER.19 (19-SPI-MOSI), U8.2 (DB13/SDI), U9.13 (SDA)
MOT4: MOT4.1, MOT4.2, U$2.2B
unnamed: C25.1, R11.2, U8.39 (CH_B0)
unnamed: ANALOG-INPUTS.8, ANG3.1, U4.3 (+IN)
unnamed: R11.1, U4.1 (VOUT), U4.4 (-IN)
unnamed: ANG3.2, R5.1
unnamed: Q2.G, R18.2
unnamed: C26.1, R12.2, U8.42 (CH_B1)
unnamed: RPI-HEADER.15 (15-GPIO3), U8.18 (BUSY/INT)
unnamed: JP7.3, U$2.MS2
unnamed: U9.21 (GPA0), U$5.DIR
unnamed: P-ON.A, R16.1
unnamed: JP7.1, U$2.MS3
unnamed: Q1.G, R17.2
unnamed: ANALOG-INPUTS.6, ANG4.1, U5.3 (+IN)
unnamed: ANALOG-INPUTS.12, ANG1.1, U2.3 (+IN)
unnamed: R9.1, U2.1 (VOUT), U2.4 (-IN)
unnamed: C23.1, R9.2, U8.33 (CH_A0)
unnamed: R12.1, U5.1 (VOUT), U5.4 (-IN)
unnamed: ANG1.2, R3.1
unnamed: ANG4.2, R6.1
unnamed: RPI-HEADER.22 (22-GPIO6), U9.18 (*RESET)
unnamed: RPI-HEADER.13 (13-GPIO2), U8.23 (CONVST_A)
unnamed: RPI-HEADER.18 (18-GPIO5), U9.19 (INTB)
unnamed: C28.1, R14.2, U8.48 (CH_C1)
unnamed: C24.1, R10.2, U8.36 (CH_A1)
unnamed: JP12.5, U$5.MS1
unnamed: Q3.G, R19.2
unnamed: JP10.5, U$6.MS1
unnamed: JP9.5, U$4.MS1
unnamed: JP8.2, JP8.4, JP8.6, R22.1
unnamed: JP7.2, JP7.4, JP7.6, R21.1
unnamed: JP12.3, U$5.MS2
unnamed: JP12.1, U$5.MS3
unnamed: U9.22 (GPA1), U$5.STEP
unnamed: R20.1, U9.2 (GPB1)
unnamed: U$2.RST, U$2.SLP (SLEEP)
unnamed: RPI-HEADER.16 (16-GPIO4), U9.20 (INTA)
unnamed: R17.1, U9.3 (GPB2)
unnamed: R18.1, U9.5 (GPB4)
unnamed: JP8.5, U$3.MS1
unnamed: RPI-HEADER.7 (7-GPIO7), U8.28 (RESET)
unnamed: JP8.3, U$3.MS2
unnamed: JP8.1, U$3.MS3
unnamed: JP9.3, U$4.MS2
unnamed: U9.23 (GPA2), U$6.DIR
unnamed: U9.24 (GPA3), U$6.STEP
unnamed: U$3.RST, U$3.SLP (SLEEP)
unnamed: Q4.G, R20.2
unnamed: JP9.1, U$4.MS3
unnamed: JP10.3, U$6.MS2
unnamed: JP10.1, U$6.MS3
unnamed: JP7.5, U$2.MS1
unnamed: LED2.A, R1.1
unnamed: LED5.A, R27.1
unnamed: JP9.2, JP9.4, JP9.6, R23.1
unnamed: JP13.2, R29.2, R30.2
unnamed: LED3.A, R15.1
unnamed: U9.25 (GPA4), U$4.DIR
unnamed: U9.26 (GPA5), U$4.STEP
unnamed: U$4.RST, U$4.SLP (SLEEP)
unnamed: I2C/UART/GPIO1.6, RPI-HEADER.10 (10-RX)
unnamed: LED4.A, R26.1
unnamed: I2C/UART/GPIO1.5, RPI-HEADER.8 (8-TX)
unnamed: I2C/UART/GPIO1.4, RPI-HEADER.2 (2-+5V)
unnamed: R30.1, RPI-HEADER.3 (3-SDA0)
unnamed: I2C/UART/GPIO1.1, R29.1, RPI-HEADER.5 (5-SCL0)
unnamed: JP12.2, JP12.4, JP12.6, R24.1
unnamed: U9.27 (GPA6), U$3.DIR
unnamed: U9.28 (GPA7), U$3.STEP
unnamed: U$5.RST, U$5.SLP (SLEEP)
unnamed: ANALOG-INPUTS.10, ANG2.1, U3.3 (+IN)
unnamed: JP14.1, R31.1, R32.1, R33.1
unnamed: R10.1, U3.1 (VOUT), U3.4 (-IN)
unnamed: ANG2.2, R4.1
unnamed: R19.1, U9.6 (GPB5)
unnamed: C27.1, R13.2, U8.45 (CH_C0)
unnamed: ANALOG-INPUTS.4, ANG5.1, U6.3 (+IN)
unnamed: U9.7 (GPB6), U$2.DIR
unnamed: U9.8 (GPB7), U$2.STEP
unnamed: JP10.2, JP10.4, JP10.6, R25.1
unnamed: U$6.RST, U$6.SLP (SLEEP)
unnamed: R13.1, U6.1 (VOUT), U6.4 (-IN)
unnamed: ANG5.2, R7.1
unnamed: ANALOG-INPUTS.2, ANG6.1, U7.3 (+IN)
unnamed: R14.1, U7.1 (VOUT), U7.4 (-IN)
unnamed: ANG6.2, R8.1
unnamed: RPI-HEADER.11 (11-GPIO0), U8.24 (~STBY)
POK: PS.3, R16.2
PON: POWER-JUMPER.1, PS.6
PWM1: D4.A, LED5.C, PWM3.1, Q2.D
PWM2: D1.A, LED2.C, PWM1.1, Q1.D
PWM3: D2.A, LED3.C, PWM4.1, Q3.D
PWM4: D3.A, LED4.C, PWM2.1, Q4.D
REFC_A: C10.1, U8.54 (REFC_A)
REFC_B: C15.1, U8.56 (REFC_B)
REFC_C: C18.1, U8.58 (REFC_C)
REFIO: C3.1, U8.51 (REFIO)

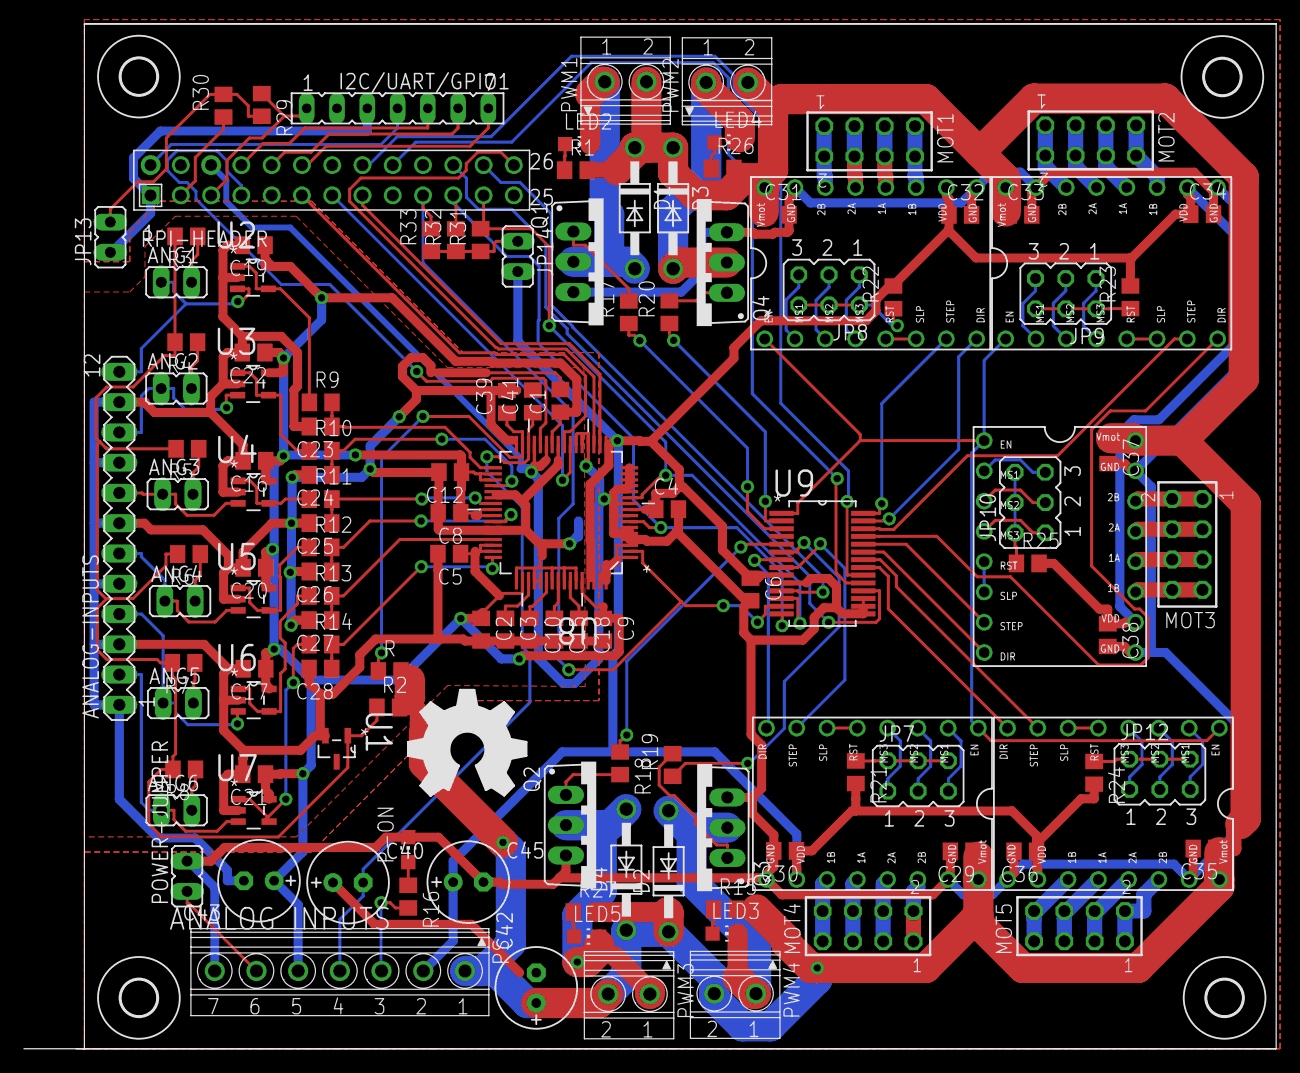
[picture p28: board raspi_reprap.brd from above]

Board: 2 copper layers, 105.1 x 86.0 mm, 133 parts (1 on the bottom side), 132 nets.

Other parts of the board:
U$7, U$8, U$9, U$10: 3,0
U$11: OSHW_FILLX350_NOTEXT

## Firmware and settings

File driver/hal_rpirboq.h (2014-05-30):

/**   Copyright (C) 2013 Rodolfo Boris Oporto Quisbert
*
*    This file is part of rpi_rboq project
*
*    Portions of this code is based on stepgen.c
*    by John Kasunich, Copyright (C) 2003-2007
*    
*    Portions of this code is based on hal_picnc.c
*    by GP Orcullo, Copyright (C) 2013
*
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
*    You should have received a copy of the GNU General Public License
*    along with this program; if not, write to the Free Software
*    Foundation, Inc., 51 Franklin St, Fifth Floor, Boston, MA  02110-1301 USA
*/

#ifndef PICNC_H
#define PICNC_H

#define SPICLKDIV_8		8	/* ~31.25MHz */
#define SPICLKDIV_16	16	/* 15.625MHz */
#define SPICLKDIV_32	32	/* ~7.8125MHz */
#define SPICLKDIV_64	64	/* ~3.90625MHz */

#define NUMAXES			4		/* X Y Z A */

#define REQ_TIMEOUT		10000ul

#define SPIBUFSIZE		32		/* SPI buffer size */
#define BUFSIZE			(SPIBUFSIZE/4)

#define STEPBIT			23		/* bit location in DDS accum */
#define STEP_MASK		(1<<STEPBIT)

#define BASEFREQ		160000ul	/* Base freq of the PIC stepgen in Hz */
#define SYS_FREQ		(80000000ul)    /* 80 MHz */

#define PERIODFP 		((double)1.0 / (double)(BASEFREQ))
#define VELSCALE		((double)STEP_MASK * PERIODFP)
#define ACCELSCALE		(VELSCALE * PERIODFP)

#define get_position(a)		(rxBuf[1 + (a)])
#define get_inputs()		(rxBuf[1 + NUMAXES])
#define set_outputs		(txBuf[1 + NUMAXES])
#define get_adc(a)		(rxBuf[2 + NUMAXES + a])
#define update_velocity(a, b)	(txBuf[1 + (a)] = (b))

/* Broadcom defines */

#define BCM2835_PERI_BASE	0x20000000
#define BCM2835_GPIO_BASE	(BCM2835_PERI_BASE + 0x200000) /* GPIO controller */
#define BCM2835_SPI_BASE	(BCM2835_PERI_BASE + 0x204000) /* SPI controller */

#define BCM2835_GPFSEL0		*(gpio)
#define BCM2835_GPFSEL1		*(gpio + 1)
#define BCM2835_GPFSEL2		*(gpio + 2)
#define BCM2835_GPFSEL3		*(gpio + 3)
#define BCM2835_GPFSEL4		*(gpio + 4)
#define BCM2835_GPFSEL5		*(gpio + 5)
#define BCM2835_GPSET0		*(gpio + 7)
#define BCM2835_GPSET1		*(gpio + 8)
#define BCM2835_GPCLR0		*(gpio + 10)
#define BCM2835_GPCLR1		*(gpio + 11)
#define BCM2835_GPLEV0		*(gpio + 13)
#define BCM2835_GPLEV1		*(gpio + 14)
#define BCM2835_GPEDS0		*(gpio + 16)
#define BCM2835_GPEDS1		*(gpio + 17)
#define BCM2835_GPREN0		*(gpio + 19)
#define BCM2835_GPREN1		*(gpio + 20)
#define BCM2835_GPFEN0		*(gpio + 22)
#define BCM2835_GPFEN1		*(gpio + 23)
#define BCM2835_GPAREN0		*(gpio + 31)
#define BCM2835_GPAREN1		*(gpio + 32)
#define BCM2835_GPAFEN0		*(gpio + 34)
#define BCM2835_GPAFEN1		*(gpio + 35)


#define BCM2835_SPICS 		*(spi + 0)
#define BCM2835_SPIFIFO     *(spi + 1)
#define BCM2835_SPICLK 		*(spi + 2)


#define SPI_CS_LEN_LONG		0x02000000
#define SPI_CS_DMA_LEN		0x01000000
#define SPI_CS_CSPOL2		0x00800000
#define SPI_CS_CSPOL1		0x00400000
#define SPI_CS_CSPOL0		0x00200000
#define SPI_CS_RXF		0x00100000
#define SPI_CS_RXR		0x00080000
#define SPI_CS_TXD		0x00040000
#define SPI_CS_RXD		0x00020000
#define SPI_CS_DONE		0x00010000
#define SPI_CS_LEN		0x00002000
#define SPI_CS_REN		0x00001000
#define SPI_CS_ADCS		0x00000800
#define SPI_CS_INTR		0x00000400
#define SPI_CS_INTD		0x00000200
#define SPI_CS_DMAEN		0x00000100
#define SPI_CS_TA		0x00000080
#define SPI_CS_CSPOL		0x00000040
#define SPI_CS_CLEAR_RX		0x00000020
#define SPI_CS_CLEAR_TX		0x00000010
#define SPI_CS_CPOL		0x00000008
#define SPI_CS_CPHA		0x00000004
#define SPI_CS_CS_10		0x00000002
#define SPI_CS_CS_01		0x00000001
#define SPI_CS_CS_00		0x00000000

#define PAGE_SIZE		(4*1024)
#define BLOCK_SIZE		(4*1024)

#define    IODIRA    (0x00)      // MCP23x17 I/O Direction Register
#define    IODIRB    (0x01)      // 1 = Input (default), 0 = Output

#define    IPOLA     (0x02)      // MCP23x17 Input Polarity Register
#define    IPOLB     (0x03)      // 0 = Normal (default)(low reads as 0), 1 = Inverted (low reads as 1)

#define    GPINTENA  (0x04)      // MCP23x17 Interrupt on Change Pin Assignements
#define    GPINTENB  (0x05)      // 0 = No Interrupt on Change (default), 1 = Interrupt on Change

#define    DEFVALA   (0x06)      // MCP23x17 Default Compare Register for Interrupt on Change
#define    DEFVALB   (0x07)      // Opposite of what is here will trigger an interrupt (default = 0)

#define    INTCONA   (0x08)      // MCP23x17 Interrupt on Change Control Register
#define    INTCONB   (0x09)      // 1 = pin is compared to DEFVAL, 0 = pin is compared to previous state (default)

#define    IOCON     (0x0A)      // MCP23x17 Configuration Register
//                   (0x0B)      //     Also Configuration Register

#define    GPPUA     (0x0C)      // MCP23x17 Weak Pull-Up Resistor Register
#define    GPPUB     (0x0D)      // INPUT ONLY: 0 = No Internal 100k Pull-Up (default) 1 = Internal 100k Pull-Up 

#define    INTFA     (0x0E)      // MCP23x17 Interrupt Flag Register
#define    INTFB     (0x0F)      // READ ONLY: 1 = This Pin Triggered the Interrupt

#define    INTCAPA   (0x10)      // MCP23x17 Interrupt Captured Value for Port Register
#define    INTCAPB   (0x11)      // READ ONLY: State of the Pin at the Time the Interrupt Occurred

#define    GPIOA     (0x12)      // MCP23x17 GPIO Port Register
#define    GPIOB     (0x13)      // Value on the Port - Writing Sets Bits in the Output Latch

#define    OLATA     (0x14)      // MCP23x17 Output Latch Register
#define    OLATB     (0x15)      // 1 = Latch High, 0 = Latch Low (default) Reading Returns Latch State, Not Port Value!

#define    MCP_ADDR      (0b00000000)  // Opcode for MCP23S17 with LSB (bit0) set to write (0), address OR'd in later, bits 1-3
#define    OPCODEW       (0b01000000)  // Opcode for MCP23S17 with LSB (bit0) set to write (0), address OR'd in later, bits 1-3
#define    OPCODER       (0b01000001)  // Opcode for MCP23S17 with LSB (bit0) set to read (1), address OR'd in later, bits 1-3
#define    ADDR_ENABLE   (0b00001000)  // Configuration register for MCP23S17, the only thing we change is enabling hardware addressing

#endif

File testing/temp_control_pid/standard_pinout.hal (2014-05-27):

# standard pinout config file for 3-axis steppers
# using a parport for I/O
#
# first load the parport driver
loadrt hal_rpirboq 
#loadrt encoder num_chan=1
loadrt pid num_chan=1
loadrt pwmgen output_type=0
loadrt not count=1

#addf parport.0.read base-thread 1
addf rpirboq.update-rpirboq base-thread 

addf rpirboq.read-rpirboq servo-thread 

#addf encoder.capture-position servo-thread
#addf encoder.update-counters base-thread
addf pid.0.do-pid-calcs servo-thread

addf pwmgen.make-pulses base-thread
addf pwmgen.update servo-thread
addf not.0 base-thread

# for temp-measurement input to pin13
#net pin13 parport.0.pin-13-in encoder.0.phase-A
#setp encoder.0.counter-mode 1 

net temp_volt rpirboq.analog.1.values pid.0.feedback

net pidout pid.0.output pwmgen.0.value
net pwmout pwmgen.0.pwm rpirboq.pwm.1.control

setp pid.0.Pgain -0.75
setp pid.0.Igain -0.1
setp pid.0.Dgain 0
setp pid.0.maxoutput 30

setp pwmgen.0.scale 1
setp pwmgen.0.pwm-freq 100
setp pwmgen.0.dither-pwm 0
setp pwmgen.0.max-dc 0.75
setp pwmgen.0.min-dc 0.0


setp rpirboq.enable-mot FALSE
#
# finally connect physical pins to the signals
net Xstep => rpirboq.servo.2.control
net Xdir  => rpirboq.servo.3.control
net Ystep => rpirboq.servo.6.control
net Ydir  => rpirboq.servo.7.control
net Zstep => rpirboq.servo.4.control
net Zdir  => rpirboq.servo.5.control

# create a signal for the estop loopback
net estop-loop iocontrol.0.user-enable-out iocontrol.0.emc-enable-in

# create signals for tool loading loopback
net tool-prep-loop iocontrol.0.tool-prepare iocontrol.0.tool-prepared
net tool-change-loop iocontrol.0.tool-change iocontrol.0.tool-changed

# connect "spindle on" motion controller pin to a physical pin
# net spindle-on motion.spindle-on => parport.0.pin-09-out

###
### You might use something like this to enable chopper drives when machine ON
### the Xen signal is defined in core_stepper.hal
###

# net Xen => parport.0.pin-01-out

###
### If you want active low for this pin, invert it like this:
###

# setp parport.0.pin-01-out-invert 1

###
### A sample home switch on the X axis (axis 0).  make a signal,
### link the incoming parport pin to the signal, then link the signal
### to EMC's axis 0 home switch input pin
###

# net Xhome parport.0.pin-10-in => axis.0.home-sw-in

###
### Shared home switches all on one parallel port pin?
### that's ok, hook the same signal to all the axes, but be sure to 
### set HOME_IS_SHARED and HOME_SEQUENCE in the ini file.  See the
### user manual!
###

# net homeswitches <= parport.0.pin-10-in
# net homeswitches => axis.0.home-sw-in
# net homeswitches => axis.1.home-sw-in
# net homeswitches => axis.2.home-sw-in

###
### Sample separate limit switches on the X axis (axis 0)
###

# net X-neg-limit parport.0.pin-11-in => axis.0.neg-lim-sw-in
# net X-pos-limit parport.0.pin-12-in => axis.0.pos-lim-sw-in

###
### Just like the shared home switches example, you can wire together
### limit switches.  Beware if you hit one, EMC will stop but can't tell
### you which switch/axis has faulted.  Use caution when recovering from this.
###

# net Xlimits parport.0.pin-13-in => axis.0.neg-lim-sw-in axis.0.pos-lim-sw-in

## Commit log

2014-05-10 First commit
    Preliminary version
    [Bottom solder mask.GBS, Bottom_cooper.GBL, Bottom_silk.GBO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]
2014-05-17 new version of driverr
    this version works perfecly with hal_meter and halscope
2014-05-17 works
    Driver works, perfectly and we upgrade just part of the register
2014-05-27 Final commit
    All documentation included presentation and report
    [core_stepper.hal, hal_test.hal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]
2014-05-30 New version
    [Bottom solder mask.GBS, Bottom_cooper.GBL, Bottom_silk.GBO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]

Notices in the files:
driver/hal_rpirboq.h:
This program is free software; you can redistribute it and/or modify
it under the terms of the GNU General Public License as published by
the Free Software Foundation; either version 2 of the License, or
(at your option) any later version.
